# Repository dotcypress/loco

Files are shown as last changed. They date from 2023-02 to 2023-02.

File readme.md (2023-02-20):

# loco

Toy CNC platform.

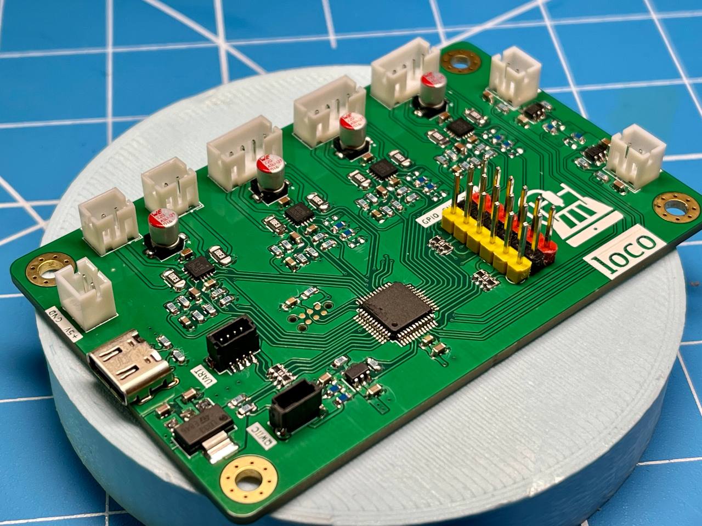
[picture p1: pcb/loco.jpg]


## License

Licensed under either of

- Apache License, Version 2.0 ([LICENSE-APACHE](LICENSE-APACHE) or
  http://www.apache.org/licenses/LICENSE-2.0)
- MIT license ([LICENSE-MIT](LICENSE-MIT) or http://opensource.org/licenses/MIT)

at your option.

### Contribution

Unless you explicitly state otherwise, any contribution intentionally submitted
for inclusion in the work by you, as defined in the Apache-2.0 license, shall be
dual licensed as above, without any additional terms or conditions.

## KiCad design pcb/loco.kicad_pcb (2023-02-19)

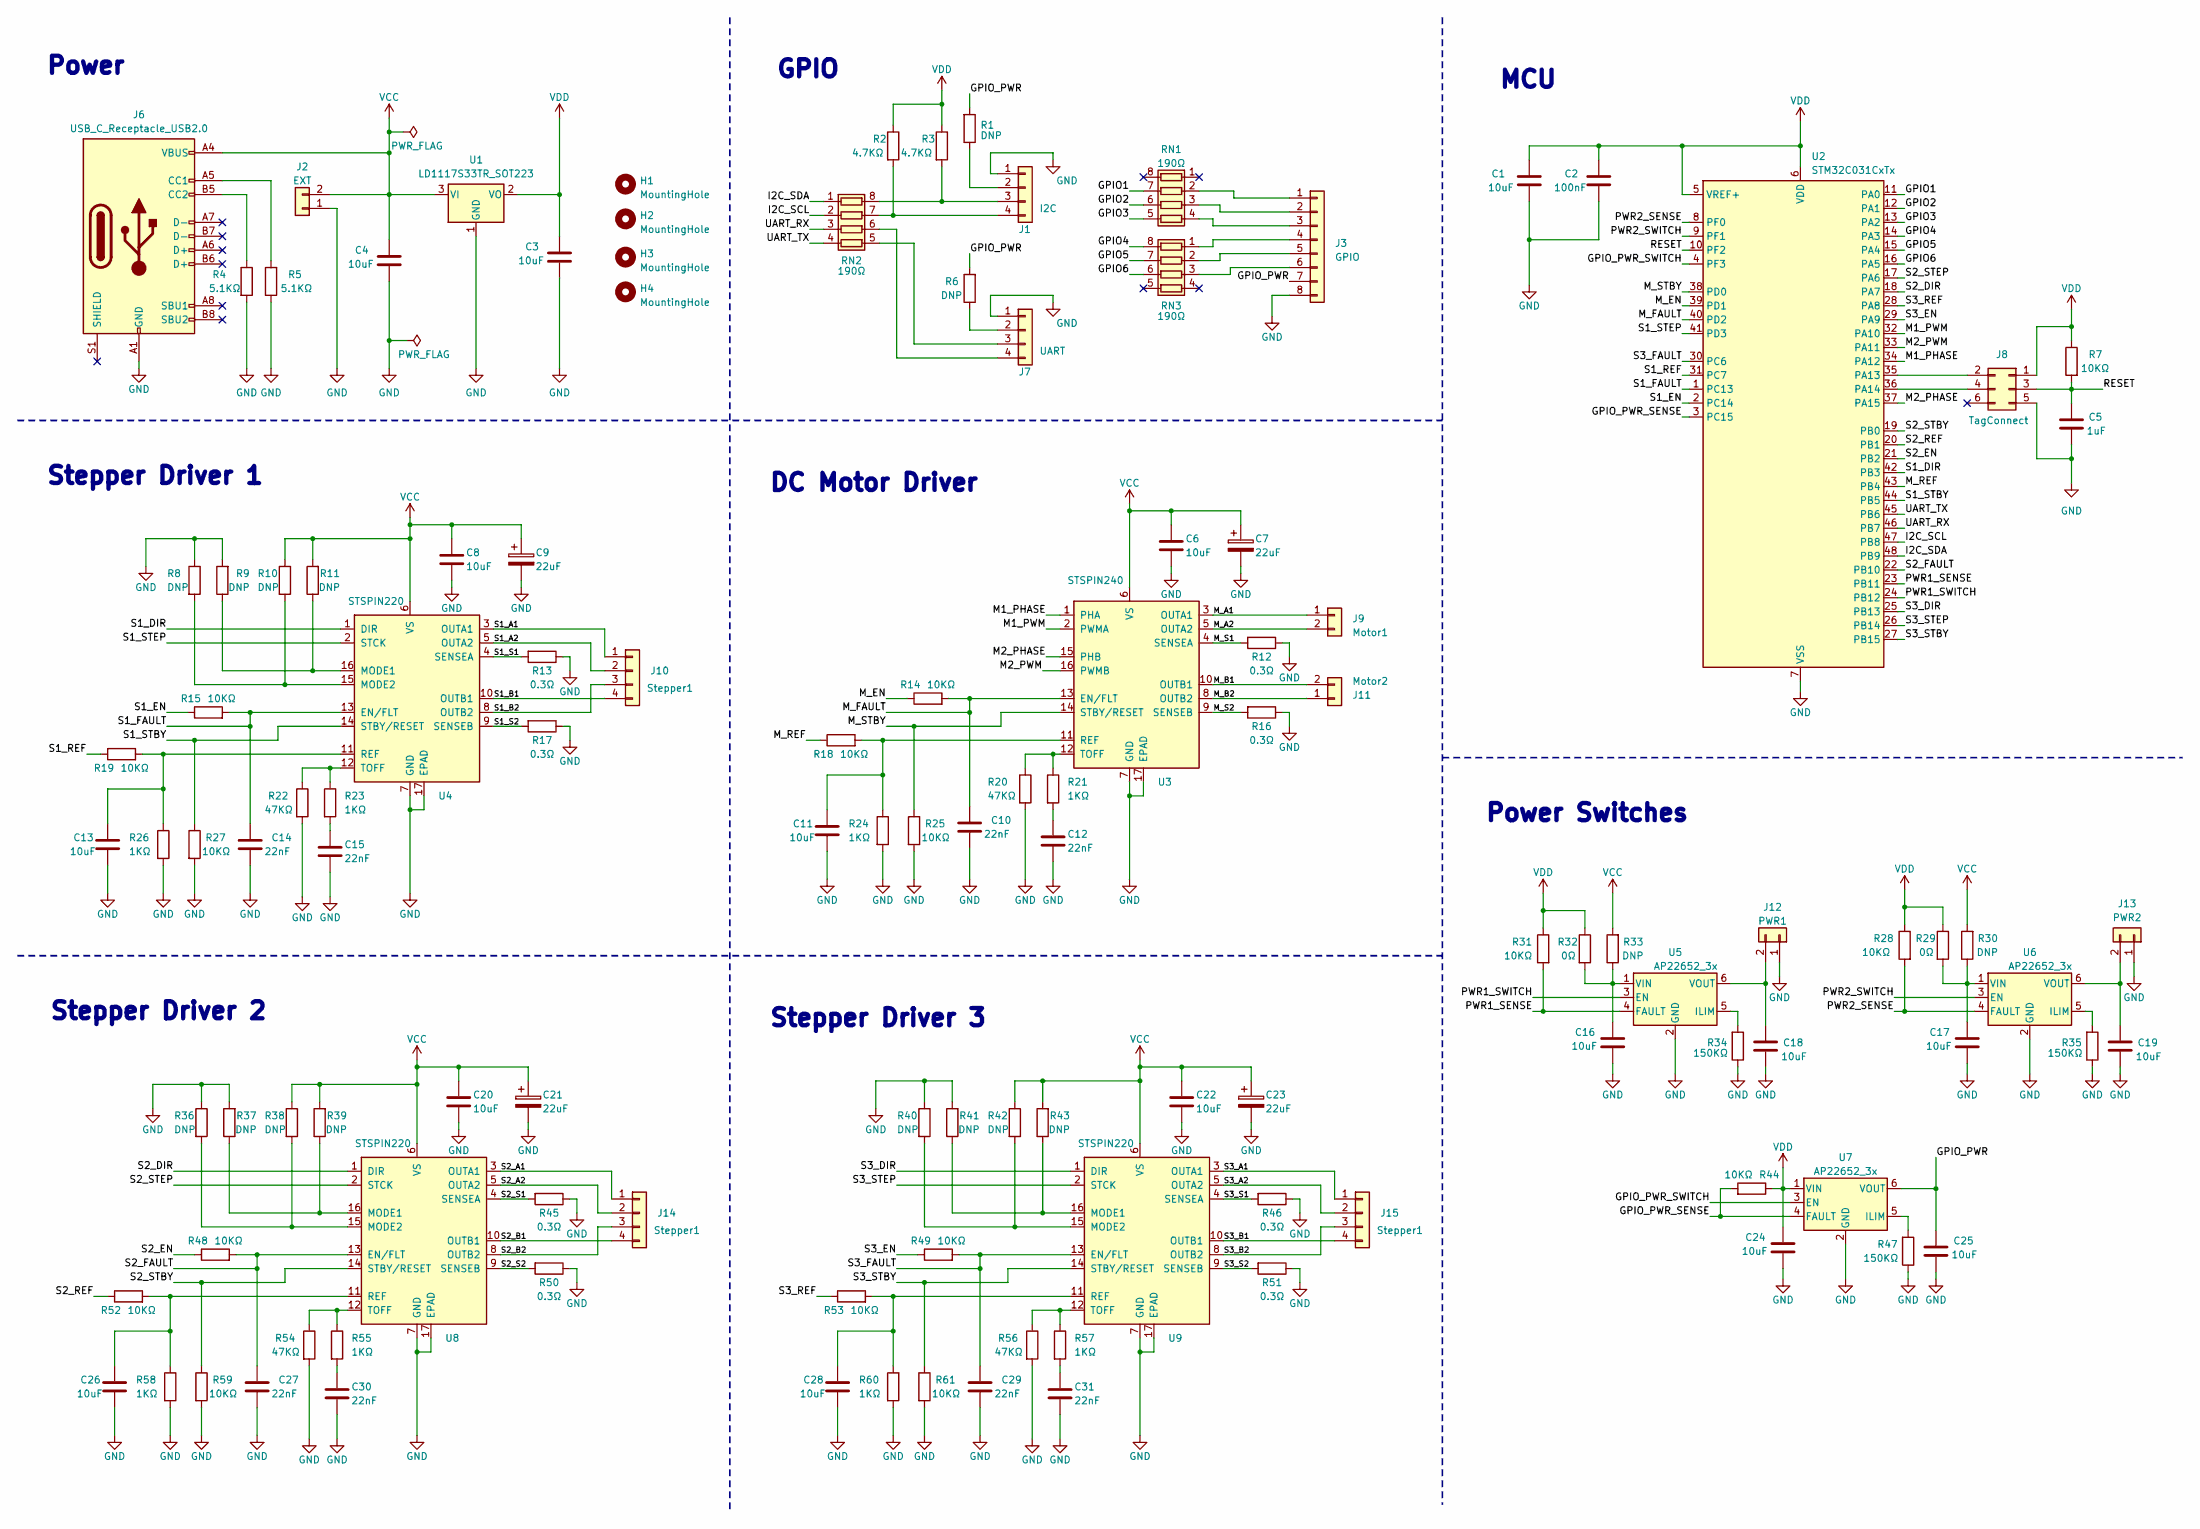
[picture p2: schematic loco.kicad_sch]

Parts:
C1, C3, C4, C6, C8, C11, C13, C16, C17, C18, C19, C20, C22, C24, C25, C26, C28: 10uF; C_0603_1608Metric
C2: 100nF; C_0603_1608Metric
C5: 1uF; C_0603_1608Metric
C7, C9, C21, C23: 22uF; CP_Elec_4x4.5
C10, C12, C14, C15, C27, C29, C30, C31: 22nF; C_0603_1608Metric
H1, H2, H3, H4: MountingHole; MountingHole_3.2mm_M3_Pad_Via
J1: I2C; JST_SH_BM04B-SRSS-TB_1x04-1MP_P1.00mm_Vertical
J2: EXT; JST_PH_B2B-PH-K_1x02_P2.00mm_Vertical
J3: GPIO; Header_03x06_P2.54mm_Vertical
J6: USB_C_Receptacle_USB2.0; USB_C_Receptacle_JAE_DX07S016JA3R1500
J7: UART; JST_SH_BM04B-SRSS-TB_1x04-1MP_P1.00mm_Vertical
J8: TagConnect; Tag-Connect_TC2030-IDC-NL_2x03_P1.27mm_Vertical
J9: Motor1; JST_PH_B2B-PH-K_1x02_P2.00mm_Vertical
J10, J14, J15: Stepper1; JST_PH_B4B-PH-K_1x04_P2.00mm_Vertical
J11: Motor2; JST_PH_B2B-PH-K_1x02_P2.00mm_Vertical
J12: PWR1; JST_PH_B2B-PH-K_1x02_P2.00mm_Vertical
J13: PWR2; JST_PH_B2B-PH-K_1x02_P2.00mm_Vertical
R1, R6, R8, R9, R10, R11, R30, R33, R36, R37, R38, R39, R40, R41, R42, R43: DNP; R_0603_1608Metric
R2, R3: 4.7KΩ; R_0603_1608Metric
R4, R5: 5.1KΩ; R_0603_1608Metric
R7, R14, R15, R18, R19, R25, R27, R28, R31, R44, R48, R49, R52, R53, R59, R61: 10KΩ; R_0603_1608Metric
R12, R13, R16, R17, R45, R46, R50, R51: 0.3Ω; R_1206_3216Metric
R20, R22, R54, R56: 47KΩ; R_0603_1608Metric
R21, R23, R24, R26, R55, R57, R58, R60: 1KΩ; R_0603_1608Metric
R29, R32: 0Ω; R_0603_1608Metric
R34, R35, R47: 150KΩ; R_0603_1608Metric
RN1, RN2, RN3: 190Ω; R_Array_Convex_4x0603
U1: LD1117S33TR_SOT223; SOT-223-3_TabPin2
U2: STM32C031CxTx; LQFP-48_7x7mm_P0.5mm
U3: STSPIN240; VQFN-16-1EP_3x3mm_P0.5mm_EP1.8x1.8mm
U4, U8, U9: STSPIN220; VQFN-16-1EP_3x3mm_P0.5mm_EP1.8x1.8mm
U5, U6, U7: AP22652_3x; SOT-23-6

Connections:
/GPIO1: RN1.7 (R2.2), U2.11 (PA0)
/GPIO2: RN1.6 (R3.2), U2.12 (PA1)
/GPIO3: RN1.5 (R4.2), U2.13 (PA2)
/GPIO4: RN3.8 (R1.2), U2.14 (PA3)
/GPIO5: RN3.7 (R2.2), U2.15 (PA4)
/GPIO6: RN3.6 (R3.2), U2.16 (PA5)
/GPIO_PWR: C25.1, J3.7, R1.2, R6.2, U7.6 (VOUT)
/GPIO_PWR_SENSE: R44.2, U2.3 (PC15), U7.4 (FAULT)
/GPIO_PWR_SWITCH: U2.4 (PF3), U7.3 (EN)
/I2C_SCL: RN2.2 (R2.1), U2.47 (PB8)
/I2C_SDA: RN2.1 (R1.1), U2.48 (PB9)
/M1_PHASE: U2.34 (PA12), U3.1 (PHA)
/M1_PWM: U2.32 (PA10), U3.2 (PWMA)
/M2_PHASE: U2.37 (PA15), U3.15 (PHB)
/M2_PWM: U2.33 (PA11), U3.16 (PWMB)
/M_A1: J9.1, U3.3 (OUTA1)
/M_A2: J9.2, U3.5 (OUTA2)
/M_B1: J11.2, U3.10 (OUTB1)
/M_B2: J11.1, U3.8 (OUTB2)
/M_EN: R14.1, U2.39 (PD1)
/M_FAULT: C10.1, R14.2, U2.40 (PD2), U3.13 (EN/FLT)
/M_REF: R18.1, U2.43 (PB4)
/M_S1: R12.2, U3.4 (SENSEA)
/M_S2: R16.2, U3.9 (SENSEB)
/M_STBY: R25.1, U2.38 (PD0), U3.14 (STBY/RESET)
/PWR1_SENSE: R31.2, U2.23 (PB11), U5.4 (FAULT)
/PWR1_SWITCH: U2.24 (PB12), U5.3 (EN)
/PWR2_SENSE: R28.2, U2.8 (PF0), U6.4 (FAULT)
/PWR2_SWITCH: U2.9 (PF1), U6.3 (EN)
/RESET: C5.1, J8.3, R7.2, U2.10 (PF2)
/S1_A1: J10.1, U4.3 (OUTA1)
/S1_A2: J10.2, U4.5 (OUTA2)
/S1_B1: J10.4, U4.10 (OUTB1)
/S1_B2: J10.3, U4.8 (OUTB2)
/S1_DIR: U2.42 (PB3), U4.1 (DIR)
/S1_EN: R15.1, U2.2 (PC14)
/S1_FAULT: C14.1, R15.2, U2.1 (PC13), U4.13 (EN/FLT)
/S1_REF: R19.1, U2.31 (PC7)
/S1_S1: R13.2, U4.4 (SENSEA)
/S1_S2: R17.2, U4.9 (SENSEB)
/S1_STBY: R27.1, U2.44 (PB5), U4.14 (STBY/RESET)
/S1_STEP: U2.41 (PD3), U4.2 (STCK)
/S2_A1: J14.1, U8.3 (OUTA1)
/S2_A2: J14.2, U8.5 (OUTA2)
/S2_B1: J14.4, U8.10 (OUTB1)
/S2_B2: J14.3, U8.8 (OUTB2)
/S2_DIR: U2.18 (PA7), U8.1 (DIR)
/S2_EN: R48.1, U2.21 (PB2)
/S2_FAULT: C27.1, R48.2, U2.22 (PB10), U8.13 (EN/FLT)
/S2_REF: R52.1, U2.20 (PB1)
/S2_S1: R45.2, U8.4 (SENSEA)
/S2_S2: R50.2, U8.9 (SENSEB)
/S2_STBY: R59.1, U2.19 (PB0), U8.14 (STBY/RESET)
/S2_STEP: U2.17 (PA6), U8.2 (STCK)
/S3_A1: J15.1, U9.3 (OUTA1)
/S3_A2: J15.2, U9.5 (OUTA2)
/S3_B1: J15.4, U9.10 (OUTB1)
/S3_B2: J15.3, U9.8 (OUTB2)
/S3_DIR: U2.25 (PB13), U9.1 (DIR)
/S3_EN: R49.1, U2.29 (PA9)
/S3_FAULT: C29.1, R49.2, U2.30 (PC6), U9.13 (EN/FLT)
/S3_REF: R53.1, U2.28 (PA8)
/S3_S1: R46.2, U9.4 (SENSEA)
/S3_S2: R51.2, U9.9 (SENSEB)
/S3_STBY: R61.1, U2.27 (PB15), U9.14 (STBY/RESET)
/S3_STEP: U2.26 (PB14), U9.2 (STCK)
/UART_RX: RN2.3 (R3.1), U2.46 (PB7)
/UART_TX: RN2.4 (R4.1), U2.45 (PB6)
GND: C1.2, C2.2, C3.2, C4.2, C5.2, C6.2, C7.2, C8.2, C9.2, C10.2, C11.2, C12.2, C13.2, C14.2, C15.2, C16.2, C17.2, C18.2, C19.2, C20.2, C21.2, C22.2, C23.2, C24.2, C25.2, C26.2, C27.2, C28.2, C29.2, C30.2, C31.2, J1.1, J2.1, J3.8, J6.A1 (GND), J7.1, J8.5, J12.1, J13.1, R4.2, R5.1, R8.1, R9.2, R12.1, R13.1, R16.1, R17.1, R20.2, R22.2, R24.2, R25.2, R26.2, R27.2, R34.1, R35.1, R36.1, R37.2, R40.1, R41.2, R45.1, R46.1, R47.1, R50.1, R51.1, R54.2, R56.2, R58.2, R59.2, R60.2, R61.2, U1.1 (GND), U2.7 (VSS), U3.7 (GND), U3.17 (EPAD), U4.7 (GND), U4.17 (EPAD), U5.2 (GND), U6.2 (GND), U7.2 (GND), U8.7 (GND), U8.17 (EPAD), U9.7 (GND), U9.17 (EPAD)
unnamed: C12.1, R21.2
unnamed: C15.1, R23.2
unnamed: C30.1, R55.2
unnamed: C31.1, R57.2
unnamed: J1.2, R1.1
unnamed: J1.3, R3.2, RN2.8 (R1.2)
unnamed: J1.4, R2.2, RN2.7 (R2.2)
unnamed: J3.1, RN1.2 (R2.1)
unnamed: J3.2, RN1.3 (R3.1)
unnamed: J3.3, RN1.4 (R4.1)
unnamed: J3.4, RN3.1 (R1.1)
unnamed: J3.5, RN3.2 (R2.1)
unnamed: J3.6, RN3.3 (R3.1)
unnamed: J6.A5 (CC1), R5.2
unnamed: J6.B5 (CC2), R4.1
unnamed: J7.2, R6.1
unnamed: J7.3, RN2.5 (R4.2)
unnamed: J7.4, RN2.6 (R3.2)
unnamed: J8.2, U2.35 (PA13)
unnamed: J8.4, U2.36 (PA14)
unnamed: C18.1, J12.2, U5.6 (VOUT)
unnamed: C19.1, J13.2, U6.6 (VOUT)
unnamed: C11.1, R18.2, R24.1, U3.11 (REF)
unnamed: R20.1, R21.1, U3.12 (TOFF)
unnamed: R9.1, R11.1, U4.16 (MODE1)
unnamed: R8.2, R10.2, U4.15 (MODE2)
unnamed: C13.1, R19.2, R26.1, U4.11 (REF)
unnamed: R22.1, R23.1, U4.12 (TOFF)
unnamed: R34.2, U5.5 (ILIM)
unnamed: C16.1, R32.2, R33.1, U5.1 (VIN)
unnamed: R35.2, U6.5 (ILIM)
unnamed: C17.1, R29.2, R30.1, U6.1 (VIN)
unnamed: R47.2, U7.5 (ILIM)
unnamed: R37.1, R39.1, U8.16 (MODE1)
unnamed: R36.2, R38.2, U8.15 (MODE2)
unnamed: C26.1, R52.2, R58.1, U8.11 (REF)
unnamed: R54.1, R55.1, U8.12 (TOFF)
unnamed: R41.1, R43.1, U9.16 (MODE1)
unnamed: R40.2, R42.2, U9.15 (MODE2)
unnamed: C28.1, R53.2, R60.1, U9.11 (REF)
unnamed: R56.1, R57.1, U9.12 (TOFF)
VCC: C4.1, C6.1, C7.1, C8.1, C9.1, C20.1, C21.1, C22.1, C23.1, J2.2, J6.A4 (VBUS), J6.A9 (VBUS), R10.1, R11.2, R30.2, R33.2, R38.1, R39.2, R42.1, R43.2, U1.3 (VI), U3.6 (VS), U4.6 (VS), U8.6 (VS), U9.6 (VS)
VDD: C1.1, C2.1, C3.1, C24.1, J8.1, R2.1, R3.1, R7.1, R28.1, R29.1, R31.1, R32.1, R44.1, U1.2 (VO), U2.5 (VREF+), U2.6 (VDD), U7.1 (VIN)

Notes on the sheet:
GPIO
Stepper Driver 3
Power Switches
Stepper Driver 1
DC Motor Driver
MCU
Power
Stepper Driver 2

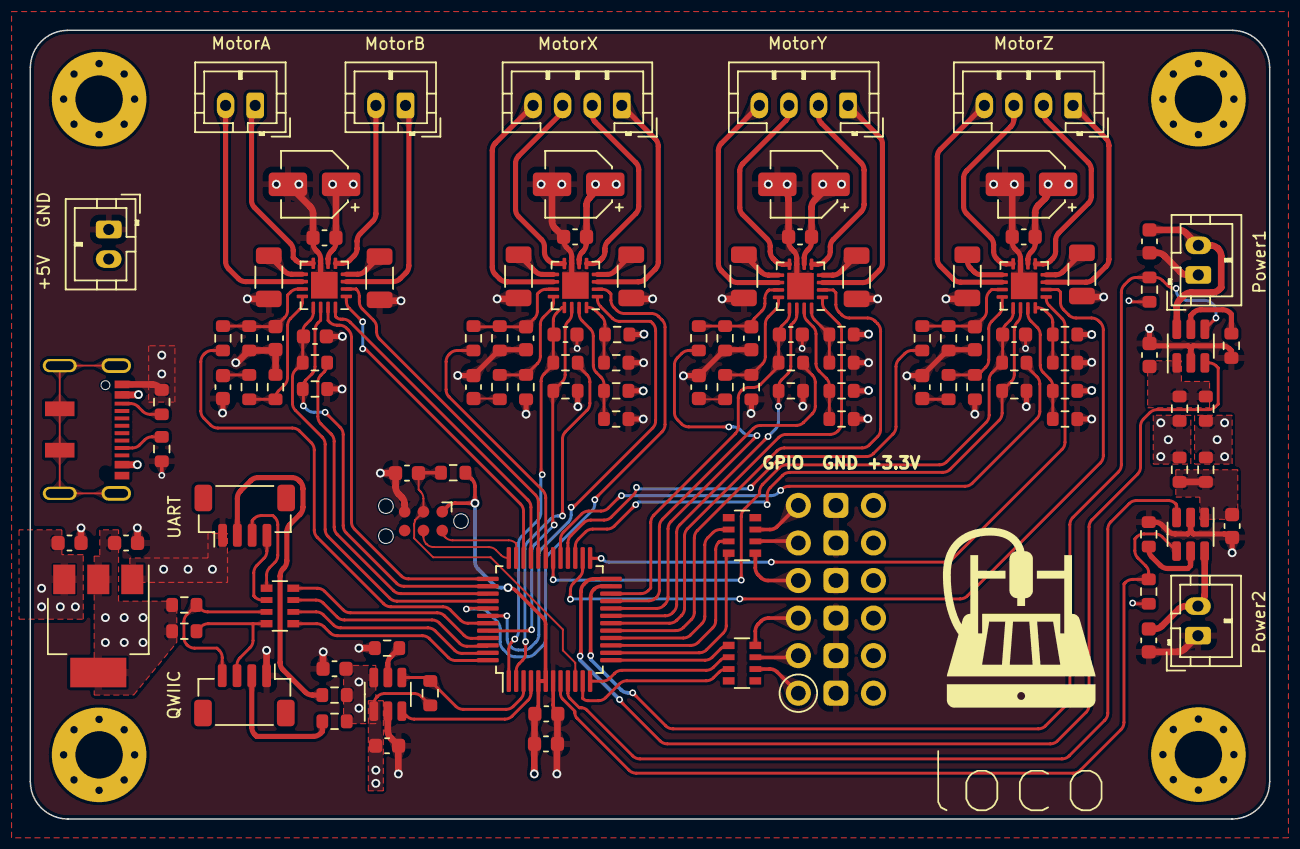
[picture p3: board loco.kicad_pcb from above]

Board: 4 copper layers, 83.8 x 53.3 mm, 121 parts (0 on the bottom side), 112 nets.

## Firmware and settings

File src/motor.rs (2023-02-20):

use crate::*;

pub enum DCMotor {
    MotorA,
    MotorB,
}
pub struct MotorController {
    phase_pins: (MotorAPhase, MotorBPhase),
    ref_pwm: PwmPin<RefTimer, timer::Channel1>,
    speed_pwm: (
        PwmPin<MotorTimer, timer::Channel4>,
        PwmPin<MotorTimer, timer::Channel3>,
    ),
    enable_pin: MotorEnable,
    standby_pin: MotorStandby,
    fault_pin: MotorFault,
    max_duty: u32,
}

impl MotorController {
    pub fn new(
        ref_pwm: PwmPin<RefTimer, timer::Channel1>,
        speed_pwm: (
            PwmPin<MotorTimer, timer::Channel4>,
            PwmPin<MotorTimer, timer::Channel3>,
        ),
        phase_pins: (MotorAPhase, MotorBPhase),
        enable_pin: MotorEnable,
        standby_pin: MotorStandby,
        fault_pin: MotorFault,
    ) -> Self {
        let max_duty = speed_pwm.0.get_max_duty() as u32;
        Self {
            speed_pwm,
            phase_pins,
            ref_pwm,
            enable_pin,
            standby_pin,
            fault_pin,
            max_duty,
        }
    }

    pub fn fault_detected(&self) -> bool {
        self.fault_pin.is_low().unwrap()
    }

    pub fn on(&mut self) {
        self.speed_pwm.0.set_duty(0);
        self.speed_pwm.0.enable();
        self.speed_pwm.1.set_duty(0);
        self.speed_pwm.1.enable();
        self.standby_pin.set_high().ok();
    }

    pub fn off(&mut self) {
        self.standby_pin.set_low().ok();
    }

    pub fn enable(&mut self) {
        self.enable_pin.set_high().ok();
    }

    pub fn disable(&mut self) {
        self.enable_pin.set_low().ok();
    }

    pub fn set_reference_voltage(&mut self, ref_v: u8) {
        let duty = self.ref_pwm.get_max_duty() as u32 * ref_v as u32 / 255;
        self.ref_pwm.set_duty(duty as _);
        self.ref_pwm.enable();
    }

    pub fn set_speed(&mut self, ch: DCMotor, val: i8) -> Status {
        let duty = self.max_duty * val.unsigned_abs() as u32 / 127;
        match ch {
            DCMotor::MotorA => {
                self.speed_pwm.0.set_duty(duty as _);
                self.phase_pins.0.set_state(val.is_negative().into()).ok();
            }
            DCMotor::MotorB => {
                self.speed_pwm.1.set_duty(duty as _);
                self.phase_pins.1.set_state(val.is_positive().into()).ok();
            }
        }
        if val == 0 {
            Status::Idle
        } else {
            Status::Busy
        }
    }
}

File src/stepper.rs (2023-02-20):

use crate::*;
use hal::hal::PwmPin;
use heapless::Deque;

#[derive(Clone, Copy, Debug)]
pub enum Job {
    Sync(usize),
    Spin(Spin),
}

#[derive(Clone, Copy, Debug)]
pub struct Spin {
    pub pulses: i32,
    pub prescaler: u8,
}

impl Spin {
    pub fn new(pulses: i32, prescaler: u8) -> Self {
        Self { pulses, prescaler }
    }
}

impl From<Spin> for Job {
    fn from(spin: Spin) -> Self {
        Job::Spin(spin)
    }
}

pub struct StepperMotor<PP, DP, EP, SP, FP, REF, const Q: usize> {
    pulse_pin: PP,
    dir_pin: DP,
    enable_pin: EP,
    standby_pin: SP,
    fault_pin: FP,
    ref_pwm: REF,
    reverse: bool,
    position: i32,
    pulses: i32,
    cnt: u8,
    prescaler: u8,
    jobs: Deque<Job, Q>,
}

impl<PP, DP, EP, SP, FP, REF, const Q: usize> StepperMotor<PP, DP, EP, SP, FP, REF, Q>
where
    PP: OutputPin,
    DP: OutputPin,
    EP: OutputPin,
    SP: OutputPin,
    FP: InputPin,
    REF: PwmPin<Duty = u32>,
{
    pub fn new(
        pulse_pin: PP,
        dir_pin: DP,
        enable_pin: EP,
        standby_pin: SP,
        fault_pin: FP,
        ref_pwm: REF,
    ) -> Self {
        Self {
            pulse_pin,
            dir_pin,
            enable_pin,
            standby_pin,
            fault_pin,
            ref_pwm,
            position: 0,
            pulses: 0,
            cnt: 0,
            prescaler: 0,
            reverse: false,
            jobs: Deque::new(),
        }
    }

    pub fn fault_detected(&self) -> bool {
        self.fault_pin.is_low().unwrap_or(true)
    }

    pub fn set_reverse(&mut self, reverse: bool) {
        self.reverse = reverse;
    }

    pub fn on(&mut self) {
        self.pulse_pin.set_low().ok();
        self.dir_pin.set_high().ok();
        self.standby_pin.set_high().ok();
    }

    pub fn off(&mut self) {
        self.standby_pin.set_low().ok();
    }

    pub fn enable(&mut self) {
        self.enable_pin.set_high().ok();
    }

    pub fn disable(&mut self) {
        self.enable_pin.set_low().ok();
    }

    pub fn set_reference_voltage(&mut self, ref_v: u8) {
        let duty = self.ref_pwm.get_max_duty() as u32 * ref_v as u32 / 255;
        self.ref_pwm.enable();
        self.ref_pwm.set_duty(duty as _);
    }

    pub fn free_space(&self) -> usize {
        Q - self.jobs.len()
    }

    pub fn push_job<J: Into<Job>>(&mut self, job: J) -> Result<(), Job> {
        self.jobs.push_back(job.into())
    }

    pub fn poll(&mut self, epoch: usize) -> Status {
        if self.fault_detected() {
            return Status::Fault;
        }

        if self.pulses != 0 {
            if self.cnt >= self.prescaler {
                let delta = self.pulses.signum();
                self.position += delta;
                self.pulses -= delta;
                self.cnt = 0;
                self.pulse_pin.set_high().ok();
            } else {
                self.cnt += 1;
                self.pulse_pin.set_low().ok();
            }
            Status::Busy
        } else {
            loop {
                match self.jobs.front() {
                    Some(Job::Spin(spin)) => {
                        self.cnt = 0;
                        self.prescaler = spin.prescaler.max(1);
                        self.pulses = if self.reverse {
                            -spin.pulses
                        } else {
                            spin.pulses
                        };
                        if self.pulses.is_positive() {
                            self.dir_pin.set_low().ok();
                        } else {
                            self.dir_pin.set_high().ok();
                        }
                        self.pulse_pin.set_low().ok();
                        self.jobs.pop_front();
                        return Status::Busy;
                    }
                    Some(Job::Sync(e)) if *e == epoch => {
                        self.jobs.pop_front();
                        continue;
                    }
                    _ => return Status::Idle,
                }
            }
        }
    }
}

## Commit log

2022-07-21 update schematics
    [loco.kicad_sch]
2022-07-28 add BOM
    [loco.kicad_pcb, loco.kicad_sch]
2022-07-29 pcb rev 0.2
    [loco.kicad_pcb, loco.kicad_sch]
2022-07-30 update motor pins
2022-07-31 add stepper driver
2022-07-31 steppert reverse
2022-08-07 pcb rev 2
    [loco.kicad_pcb]
2022-08-29 fix pull-down for spi flash
    [loco.kicad_pcb, loco.kicad_sch]
2023-01-20 editor config
    [loco.kicad_sch]
2023-02-05 pcb rev.0x03
    [loco.kicad_pcb, loco.kicad_sch]
2023-02-16 stepper motor control
2023-02-17 add dc motor driver
    [loco.kicad_sch]
2023-02-19 rev 0x04
    [loco.kicad_pcb, loco.kicad_sch]
2023-02-20 update motor controller
